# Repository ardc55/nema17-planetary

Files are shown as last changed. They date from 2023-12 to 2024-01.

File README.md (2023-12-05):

# nema17-planetary



A 2-stage, 28:1 Planetary Gearbox made for the NEMA 17 standard.
Uses mainly 3D-printed parts as well as some additional hardware to make a simple and inexpensive gearbox.

## Mechanical Overview

#### Motor Selection
For the motor to be compatible, it should have similar dimensions to this base diagram:

#### Features and internal gearing

- Decent backlash/repeatability

- All gears are helical with a helix angle of 20°

Stage 1 
7:1 Ratio 

- Planet Teeth - 30
- Sun Teeth - 12
- Ring Teeth - 72

Small teeth at higher speed -> reduce backlash inherent in multistage planetary gearings.

Stage 2
4:1 Ratio
- Planet Teeth - 12
- Sun Teeth - 12
- Ring Teeth - 36

Larger teeth at a lower speed -> higher mechanical strength, increase in max torque without damage bottleneck.

## 3D printing and settings
- All parts are confirmed to be 3D-printable in PLA with a 0.4mm nozzle

- Depending on the size and stall torque of your motor, parts such as the carriers and gears should ideally be printed at a high infill (50%-100%)
  - This version was tested with a smaller motor of length 42mm and achieved around 4Nm output torque (where skipped steps ocurr)

- For ideal performance and smooth operation, use a minimal layer height (0.1mm - 0.2mm) for all components which contain gears)

- Support required on carrier components which transmit rotation to next stage or output

## Additional Components
19x m3 Bolts of various sizes:
- 4x m3 x 10
- 10x m3 x 12
- 5x m3 x 20

5x heat-set inserts for M3 bolts on output hub, must fit rough size of 4.3mm diameter by 6.5mm depth

Grease
- Ideally, use lithium grease on all gears and shafts

## Notes/Future Plans
Additions coming soon:
Motor-mounted driver/encoder combo for active feedback

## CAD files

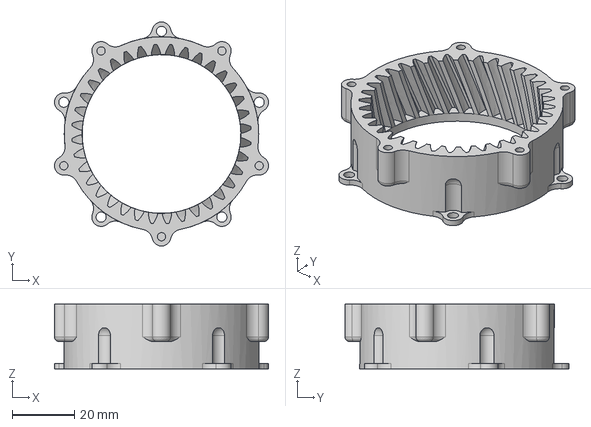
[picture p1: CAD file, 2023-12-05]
1-3DFiles/STEP/LowRedHousingHel.step
68.8 x 72.0 x 20.8 mm

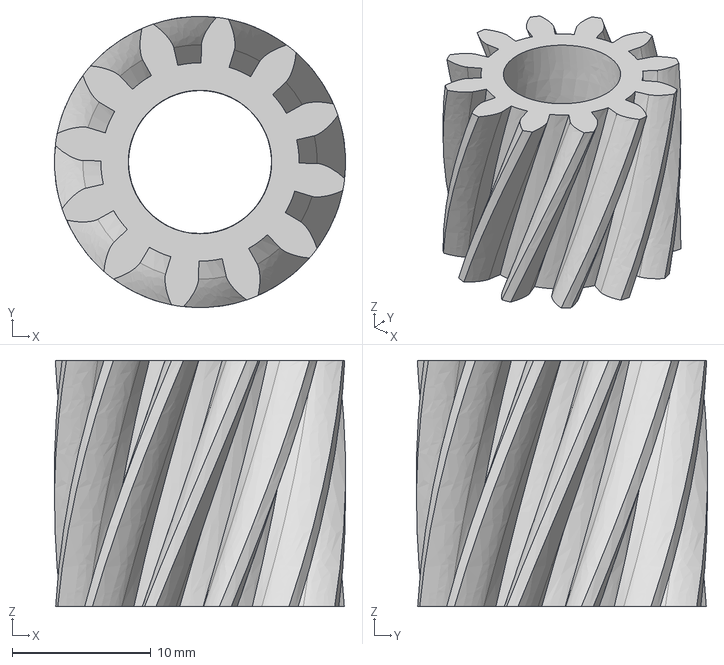
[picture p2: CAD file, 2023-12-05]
1-3DFiles/STEP/GearCoarseHel.step
21.0 x 21.0 x 17.8 mm

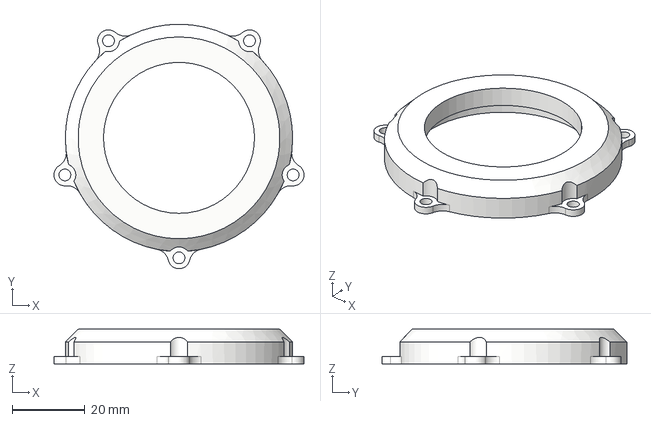
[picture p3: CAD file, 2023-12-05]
1-3DFiles/STEP/Top.step
68.8 x 67.2 x 9.50 mm

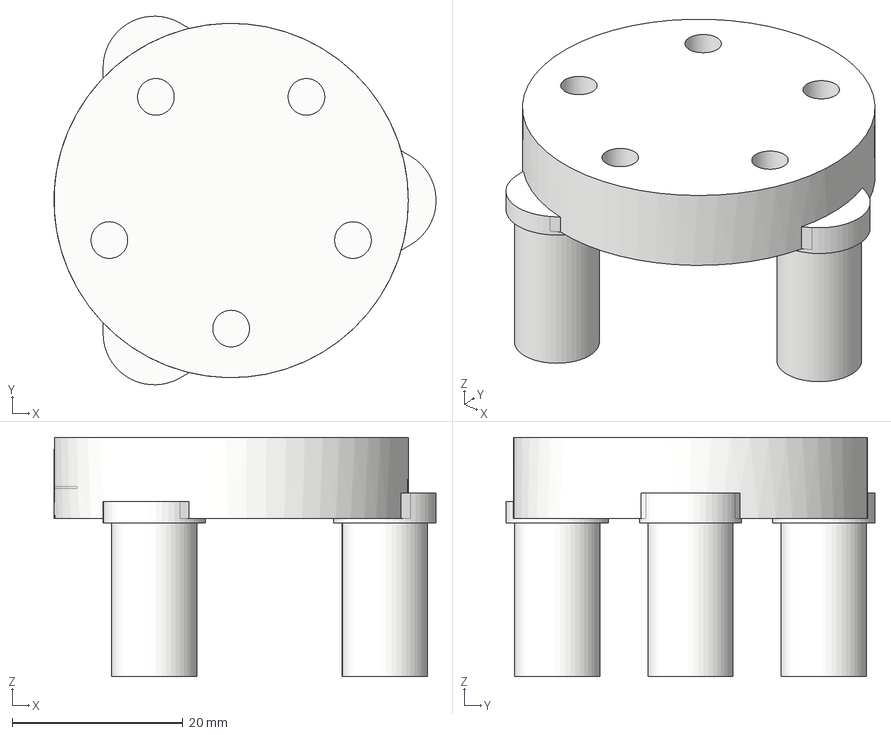
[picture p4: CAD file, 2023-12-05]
1-3DFiles/STEP/OutputCarrier.step
44.7 x 43.2 x 28.0 mm

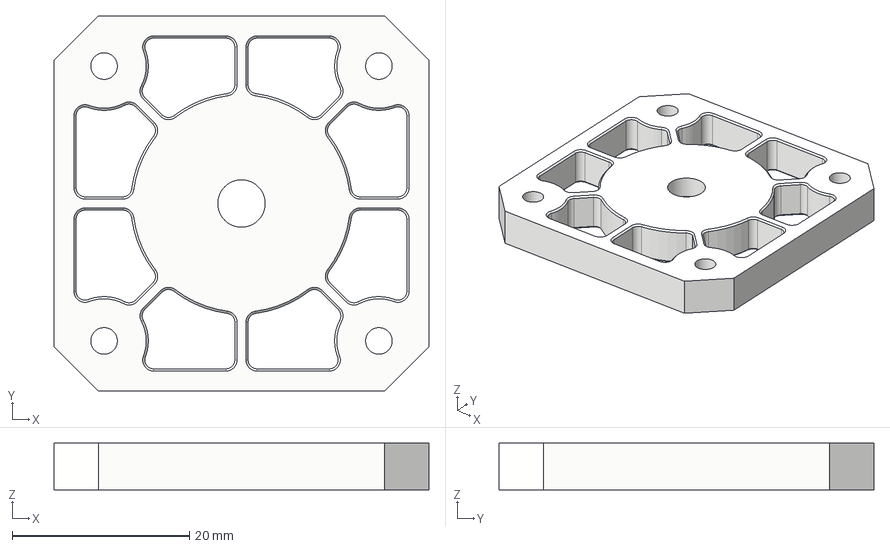
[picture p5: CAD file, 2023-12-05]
1-3DFiles/STEP/MotorHeader.step
42.3 x 42.3 x 5.25 mm

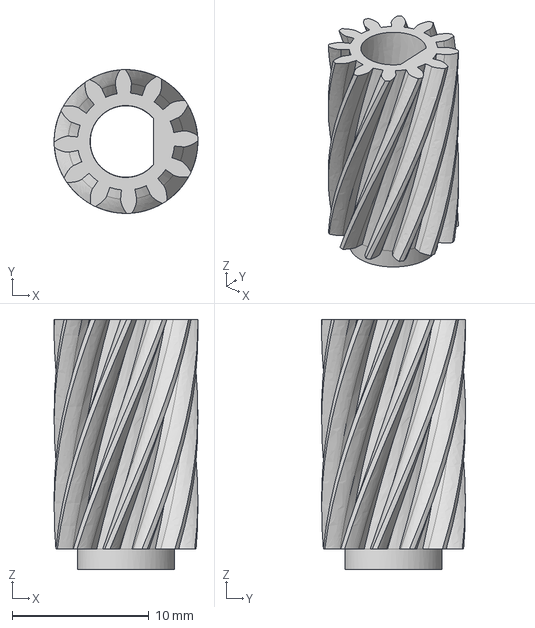
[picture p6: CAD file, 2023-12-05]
1-3DFiles/STEP/InputGearHel.step
10.5 x 10.5 x 18.3 mm

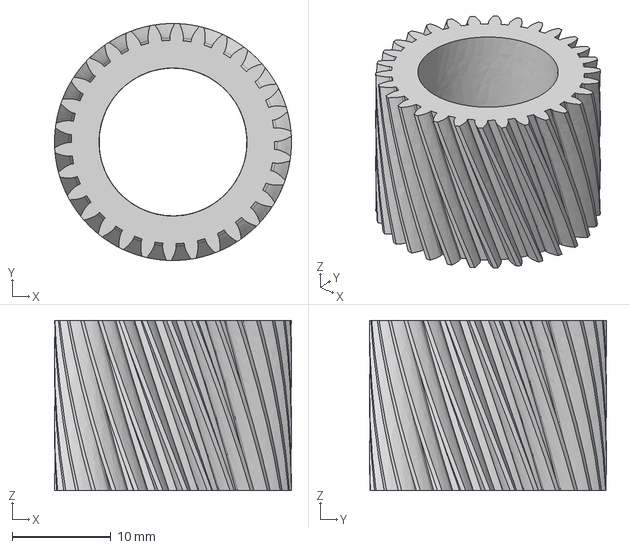
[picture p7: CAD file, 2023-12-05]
1-3DFiles/STEP/GearFineHel.step
24.0 x 24.0 x 17.2 mm

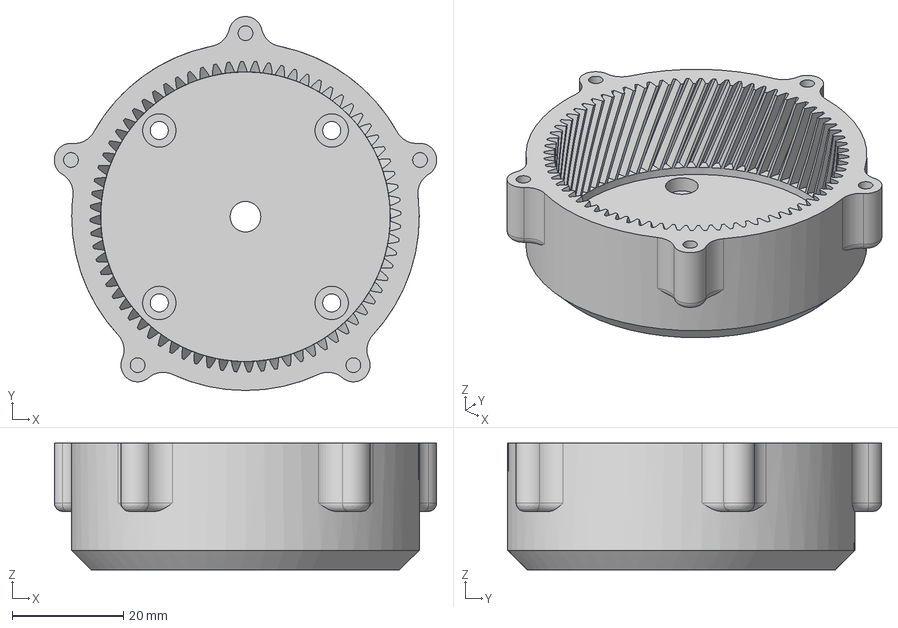
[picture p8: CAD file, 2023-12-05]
1-3DFiles/STEP/HighRedHousingHel.step
68.8 x 67.3 x 22.8 mm

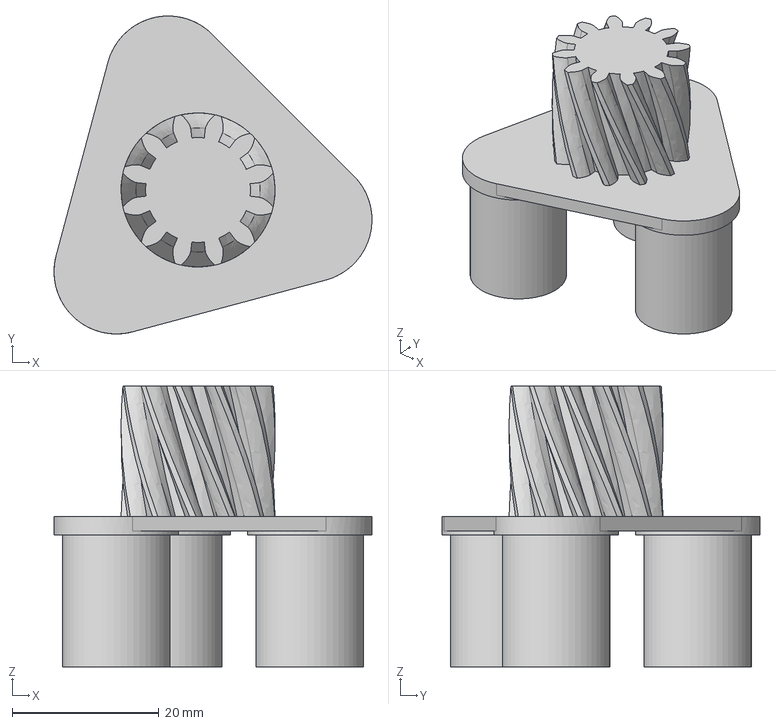
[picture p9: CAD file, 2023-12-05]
1-3DFiles/STEP/SunCarrierHel.step
43.3 x 43.3 x 38.2 mm

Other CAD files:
1-3DFiles/STL/GearCoarseHel.stl
1-3DFiles/STL/GearFineHel.stl
1-3DFiles/STL/HighRedHousingHel.stl
1-3DFiles/STL/InputGearHel.stl
1-3DFiles/STL/LowRedHousingHel.stl
1-3DFiles/STL/MotorHeader.stl
1-3DFiles/STL/OutputCarrier.stl
1-3DFiles/STL/SunCarrierHel.stl
1-3DFiles/STL/Top.stl

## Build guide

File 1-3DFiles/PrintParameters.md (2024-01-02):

## General Printing Notes

The specific accuracy of your printer can greatly affect the outcome of the gearbox and how it fits together, resulting in either too much backlash or parts that do not not fit together. 
If your printer is inaccurate, especially in the x and y axes, consider better calibrating your machine or using settings such as horizontal expansion and horizontal hole expansion with positive or negative values(Ultimater Cura) or equivalents for other slicers.

## Individual slicing and printing settings for each component

## 1. GearFineHel.stl

Description:

Fine toothed helical planetary gears (30 teeth), for first stage

Settings:

- Qty: 3
- 0.1-0.2mm layer height
- 0.4mm nozzle
- Slow print speeds (50mm/s)
- PLA
- No support required

## 2. GearCoarseHel.stl

Description:

Coarse toothed helical planetary gears (12 teeth), for second stage

Settings:

- Qty: 3
- 0.1-0.2mm layer height
- 0.4mm nozzle
- Slow print speeds (50mm/s)
- PLA
- No support required

## 3. HighRedHousingHel.stl

Description:

Fine toothed helical planetary housing (72 teeth), for first stage

Settings:

- Qty: 1
- 0.1-0.2mm layer height
- 0.4mm nozzle
- Slow print speeds (50mm/s)
- PLA
- Minimal support beneficial for overhanging area for screws to connect second stage housing

## 4. LowRedHousingHel.stl

Description:

Coarse toothed helical planetary housing (36 teeth), for second stage

Settings:

- Qty: 1
- 0.1-0.2mm layer height
- 0.4mm nozzle
- Slow print speeds (50mm/s)
- PLA
- Minimal support beneficial for overhanging area for screws to connect top

## 5. InputGearHel.stl

Description:

Input sun gear connecting motor output shaft to first stage (12 teeth)

Settings:

- Qty: 1
- 0.1-0.2mm layer height
- 0.4mm nozzle
- Slow print speeds (50mm/s)
- PLA
- No support required

## 6. SunCarrierHel.stl

Description:
First carrier, connecting the output of the first stage to the second stage (serves as a sun gear for the second stage)

Settings:

- Qty: 1
- 0.1-0.2mm layer height
- 0.4mm nozzle
- Slow print speeds (50mm/s)
- PLA
- High support required 

## 7. MotorHeader.stl

Description:

Spacer which creates between the motor and the gearbox (for small protruding section on NEMA motors)

Settings:

- Qty: 1
- 0.1-0.2mm layer height
- 0.4mm nozzle
- Slow print speeds (50mm/s)
- PLA
- No support required

## 8. Top.stl

Description:

Top plate which constrains output carrier using a lip and finalizes the assembly of the gearbox

Settings:

- Qty: 1
- 0.1-0.2mm layer height
- 0.4mm nozzle
- Slow print speeds (50mm/s)
- PLA
- Minimal support required

## 9. OutputCarier

Description:

Output carrier which takes output from second stage and delivers it to load through heat-sink inserts

Settings:

- Qty: 1
- 0.1-0.2mm layer height
- 0.4mm nozzle
- Slow print speeds (50mm/s)
- PLA
- Large support required

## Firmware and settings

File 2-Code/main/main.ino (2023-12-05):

//Created by Joshua Yaacoub, 2023
//NOTES
//Made for interfacing with a TB6600 stepper motor driver to drive a nema 17 stepper motor
//Using delayMicroseconds() for now, may update to micros() in the future for multitasking
//Contains a variety of functions which can be used with the 2 pin connections from the arduino to the driver, mostly by manipulating the pulse pin (PUL_PIN)
  
  //Interface pins
  const int DIR_PIN = 3;
  const int PUL_PIN = 4;

  //Motor gear reduction and microstepping information
  const int ratio = 28;
  const int steps = 1600; 
  const int stepsPRev = ratio*steps;

  //Used for moveTo function
  int absPos = 0;


  void setup() {
    pinMode(DIR_PIN,OUTPUT);
    pinMode(PUL_PIN,OUTPUT);
    Serial.begin(9600);
  }

//Basic - move the motor a number of steps
  void move(int steps, int dT){
    for(int x=0;x<steps;x++){
      digitalWrite(PUL_PIN,HIGH);
      delayMicroseconds(dT);
      digitalWrite(PUL_PIN,LOW);
    }
  }

//Oscillate by a number of steps and speeds in both directions
  void osc(int steps1, int dT1, int steps2, int dT2){
    digitalWrite(DIR_PIN,HIGH);
    move(steps1,dT1);
    digitalWrite(DIR_PIN,LOW);
    move(steps2,dT2);  

  }

//Quadratic acceleration function for smooth acceleration
  void quadAcc(int totalSteps, int dT1, int dT2){
    int halfsteps = totalSteps/2;
    int r = dT1-dT2;
    int dT;

    for(double x=0;x<0.5;x = x + 1.0/totalSteps){
      dT = -1*r*(pow(1.414*x,2)) + dT2 + r;
      digitalWrite(PUL_PIN,HIGH);
      delayMicroseconds(dT) ;
      digitalWrite(PUL_PIN,LOW);
      
    }
    for(double x=0.5;x<1;x+= 1.0/totalSteps){
      dT = r*(pow(1.414*(x-1),2)) + dT2;
      digitalWrite(PUL_PIN,HIGH);
      delayMicroseconds(dT);
      digitalWrite(PUL_PIN,LOW);
      
    }
  }

//Linear Acceleration (lerp) function for acceleration
  void linAcc(int totalSteps, int dT1, int dT2){
    int dT;
    float divFac = totalSteps;
    for(int x=0;x<totalSteps;x++){
      dT = dT1 + (dT2-dT1)*(x/divFac);
      digitalWrite(PUL_PIN,HIGH);
      delayMicroseconds(dT);
      digitalWrite(PUL_PIN,LOW);
    }

  }

//Enable motor (holding torque)
  void lock(){
    digitalWrite(PUL_PIN,HIGH);
  }

//Disable motor
  void unlock(){
    digitalWrite(PUL_PIN,LOW);
  }


//Move the motor a predefined angle
  void moveAngle(double angle, int dT){
    for(int x=0;x<(stepsPRev * (angle/360.0)); x++){
      digitalWrite(PUL_PIN,HIGH);
      delayMicroseconds(dT);
      digitalWrite(PUL_PIN,LOW);      
  }
}

//Move the motor to a target position
void moveTo(int target, int mdT){
  target*=16;
  for(int x=0;x<abs(target-absPos)-32;x++){
      digitalWrite(PUL_PIN,HIGH);
      if(abs(target-absPos) < 200 && abs(target-absPos) > 100){
        delayMicroseconds(mdT*2);
      }

      else if(abs(target-absPos) < 100 && abs(target-absPos) > 50){
        delayMicroseconds(mdT*3);
      }

      else if(abs(target-absPos) < 50 && abs(target-absPos) > 0){
        delayMicroseconds(mdT*4);
      }

      else{
        delayMicroseconds(mdT);
      }
      
      digitalWrite(PUL_PIN,LOW);
      if(target>absPos){
        absPos++;
        digitalWrite(DIR_PIN,HIGH);
        
      }
      if(target<absPos){
        absPos--;
        digitalWrite(DIR_PIN,LOW);
      }
    }
}


  //Place commands here
  void run(){
    //Example moveTo function, using a potentiometer as input on pin A1
    moveTo(analogRead(A1),100);
  }






  void loop() {
    run();
  }
